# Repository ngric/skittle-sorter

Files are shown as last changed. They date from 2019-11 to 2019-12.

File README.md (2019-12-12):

# skittle-sorter

complete

## Schematics

Not so good schematic:

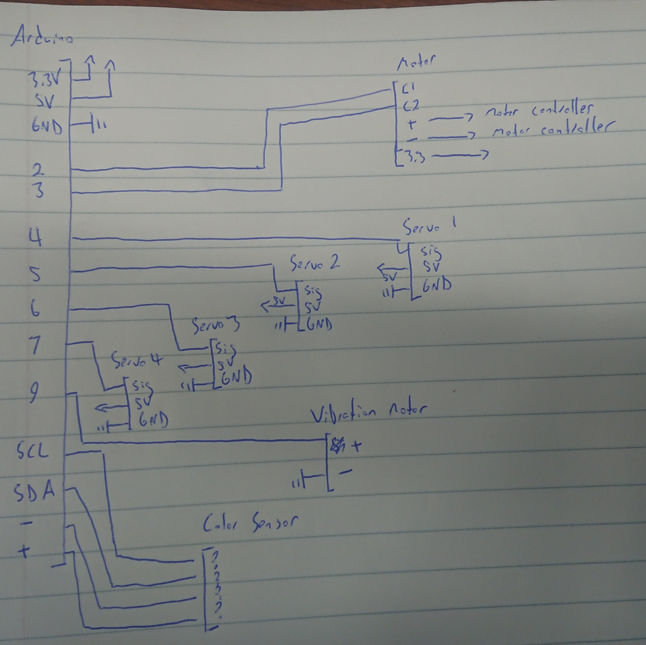
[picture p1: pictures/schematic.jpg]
schematic


Wired up:



## Auger

The centerpiece of our design was an auger, or screw of archimedes.  The skittles were supposed to be carried down a path by the auger, and then get dropped out into thier specific bins.

We went through a couple different revisions of the auger, changing the number of flights and the amount of twist. What we settled on had thwee flights, and 1500 degrees of twist. As it was too long for us to print in one piece, we split it in half then glued them together.

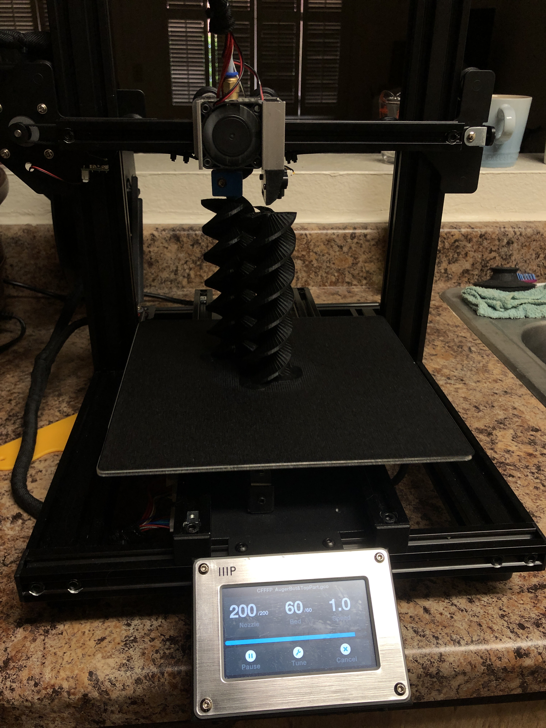
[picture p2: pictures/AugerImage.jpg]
auger printing


## Tube

The auger was contained within a tube.

The tube was split into two parts, as well, not due to length but complexity of design. The bottom section contained a hole that skittles fell into to get sorted, and an enclosure for the color sensor. The top part of the tube had four doors that skittles of specific colors were supposed to fall through.

doors

Each door needed some guides so that it would properly seat into the tube

augerthroughdoor

## Color Sensor

sensor

Our color sensor was placed at the bottom of the auger tube.
We had a lot of issues getting the sensor to read skittle color reliably. With no skittles in the chamber, we would often get readings for colors at random, regardless of how much calibration we attempted to do. Near the deadline, we found out that the sensor was starved for light, and were able to make some improvements by increasing the sensor's integration time, but we didn't get it 100% reliable. If we were to continue working on the sorter, we would likely try out different sensor chambers, and/or continue messing with the integration time, though increasing it significantly slowed down our _potential_ top sorting speed.

## Motor

The auger was powered by an encoded dc motor. Using it, we were able to count the number of steps it took for something on a specific flight of the auger to travel from the color sensor to any given door.

motor

To time it, we kept a "queue" of upcoming skittles, and the doors that should be open at any given time. Unfortunately, due to color sensing issues, we were never able to really test out the queueing.

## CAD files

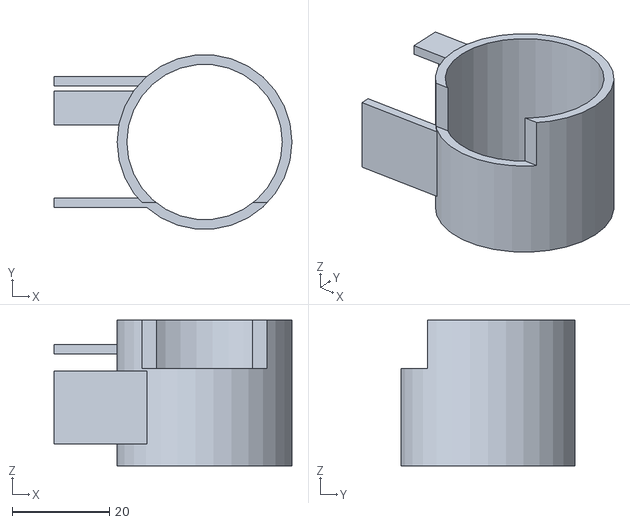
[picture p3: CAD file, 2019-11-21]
scad/clip_test_1.stl
49.0 x 35.8 x 30.0

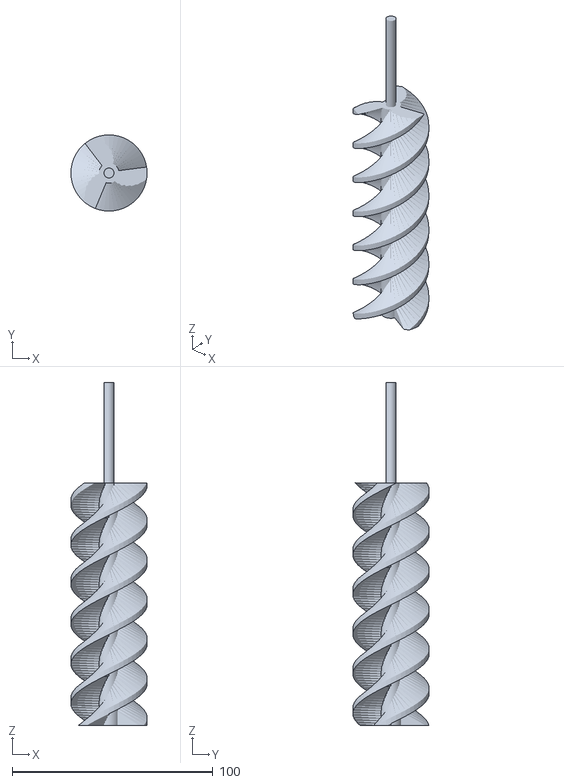
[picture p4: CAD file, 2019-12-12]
stl/AugerBotPart.stl
38.0 x 38.0 x 171.0

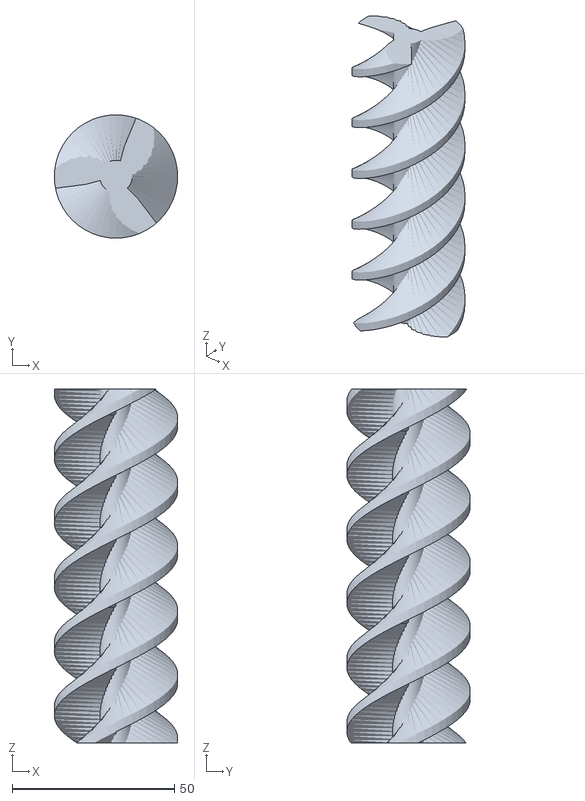
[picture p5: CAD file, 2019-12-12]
stl/AugerTopPart.stl
38.0 x 38.0 x 109.0

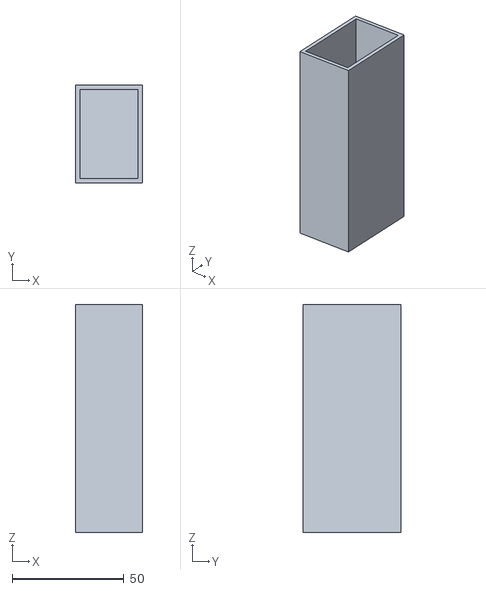
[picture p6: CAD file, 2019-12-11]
stl/SkittleBox.stl
30.0 x 44.0 x 102.0

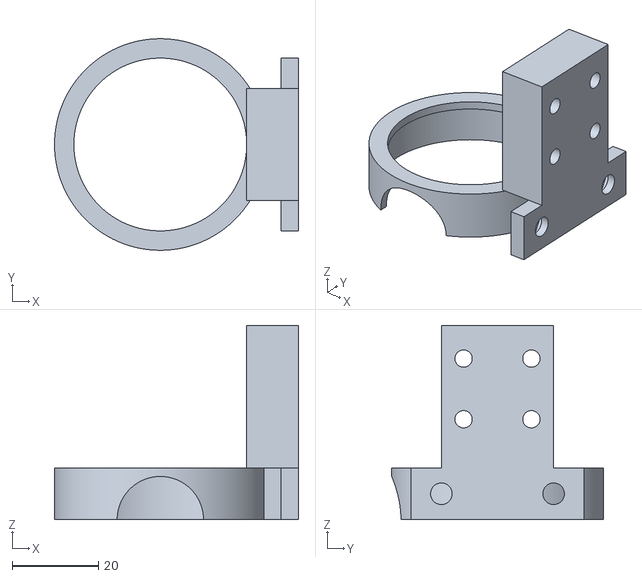
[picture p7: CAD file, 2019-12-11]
stl/motorSideMount.stl
56.5 x 49.0 x 45.0

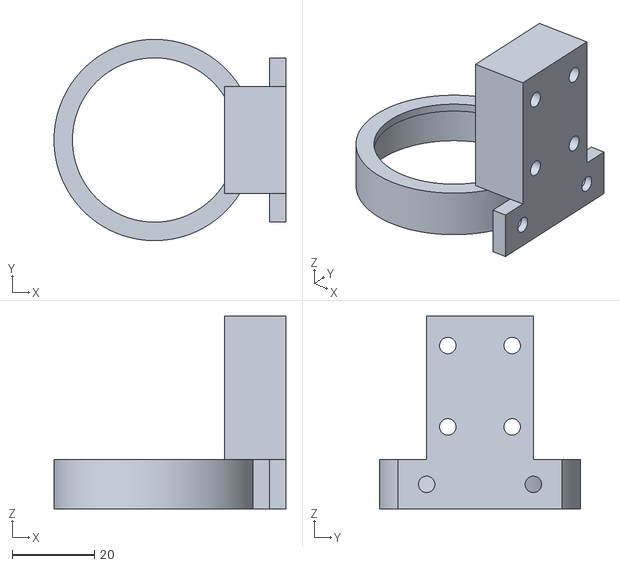
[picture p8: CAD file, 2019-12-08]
stl/mounts.stl
56.5 x 49.0 x 47.0

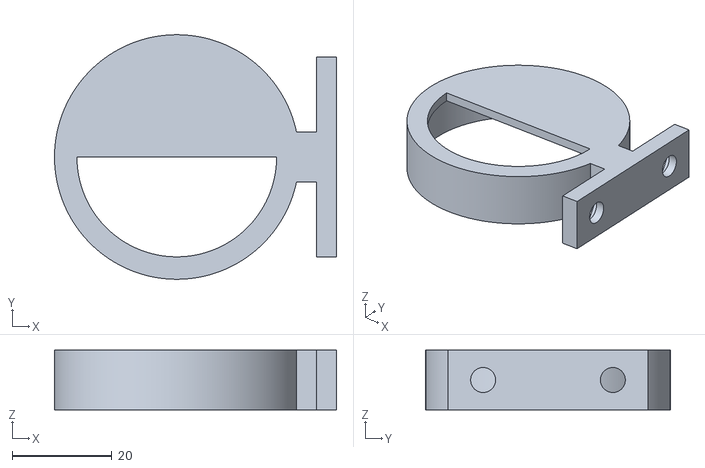
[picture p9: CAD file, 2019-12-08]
stl/augerSideMount.stl
56.5 x 49.0 x 12.0

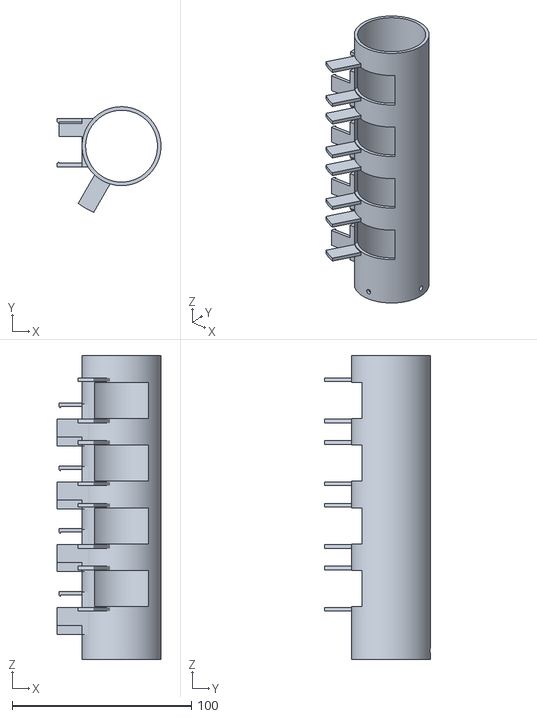
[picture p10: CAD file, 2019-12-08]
stl/tubev2.1.stl
58.0 x 58.9 x 169.5

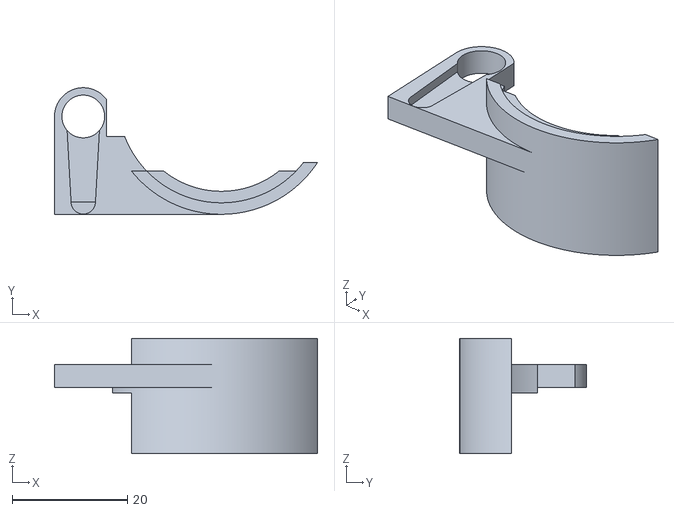
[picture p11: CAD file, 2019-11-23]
stl/door.stl
45.7 x 22.0 x 20.0

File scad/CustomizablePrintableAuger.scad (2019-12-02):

// Parametric Printable Auger
// It is licensed under the Creative Commons - GNU GPL license.
// � 2013 by William Gibson
// http://www.thingiverse.com/thing:96462

// 5 colors in skittle bag

////////////
//Examples//
////////////

//Simple Example
// auger(r1=1/8*inch, r2=.75*inch, h=1*inch, 
// turns=2, multiStart=1, flightThickness = 0.6, 
// overhangAngle=20, supportThickness=0.0);

//Multistart example
// auger(r1=1/2*inch, r2=2*inch, h=2*inch, 
// turns=1, multiStart=3, flightThickness = 0.6, 
// overhangAngle=20, supportThickness=0.0);

//Support
// auger(r1=1/2*inch, r2=2*inch, h=2*inch, 
// turns=2, multiStart=1, flightThickness = 0.6, 
// overhangAngle=10, supportThickness=0.4);


//////////////////////
//CUSTOMIZER OPTIONS//
//////////////////////

/* [Auger] */

//The total amount of twist, in degrees
Auger_twist = 1080; //[90:1080]

//The radius of the auger's "flight" past the shaft
Auger_flight_radius = 14; //[5:50]                         // == diameter of a single skittle 

//The number of "flights" 
Auger_num_flights = 3; //[1:5]

//The height, from top to bottom of the "shaft"
Auger_flight_length = 180; //[10:200]                           

/* [Printer] */

//The overhang angle your printer is capable of
Printer_overhang_capability = 30; //[0:40]

//The thickness of perimeter support material
Auger_perimeter_thickness = 0.0; //[0:None, 0.8:Thin, 2:Thick]

/* [Uninteresting] */

//The radius of the auger's "shaft"
Auger_shaft_radius = 5; //[1:25]

//The thickness of the "flight" (in the direction of height)
Auger_flight_thickness = 3;  //[0.2:Thin, 1:Medium, 10:Thick]

Auger_handedness = "right";  //["right":Right, "left":Left]

/* [Build plate] */

//for display only, doesn't contribute to final object
build_plate_selector = 3; //[0:Replicator 2,1: Replicator,2:Thingomatic,3:Manual]
//when Build Plate Selector is set to "manual" this controls the build plate x dimension
build_plate_manual_x = 200; //[100:400]
//when Build Plate Selector is set to "manual" this controls the build plate y dimension
build_plate_manual_y = 200; //[100:400]

build_plate(build_plate_selector,build_plate_manual_x,build_plate_manual_y);

/* [Hidden] */

M_PI = 3.14159;
mm = 1;
inch = 25.4 * mm;

/*---Code by Chaoneng Quan---*/
$fn = 200;
tubeHeight= Auger_flight_length - 25;


shieldHeight = 27;  //27 touching top
openRadius = 8;
openHeight = 10;


/*---end of code---*/

translate([0,0,3]) {
    difference() {
        union() {
            translate([0,0,179])rotate([180,0,0])
            auger(
                    r1 = Auger_shaft_radius,
                    r2 = Auger_shaft_radius + Auger_flight_radius,
                    h = Auger_flight_length,
                    overhangAngle = Printer_overhang_capability,
                    multiStart = Auger_num_flights,
                    flightThickness = Auger_flight_thickness,
                    turns = Auger_twist/360,
                    pitch=0,
                    supportThickness = Auger_perimeter_thickness,
                    handedness=Auger_handedness,
                    //$fn=50,
                    $fa=12,
                    $fs=5
                 );
            translate([0,0,-2])cylinder(h=3,d=5.5);
        }
        // motor shaft hole
        translate([0,0,-1])
            scale([1.05,1.05,1.05]){
                difference() {
                    translate([0,0,-3])
                        cylinder(h=15,d=4);
                    translate([1.5,-2,-3])
                        cube([4,4,15]);
                }
            }
        translate([0,0,179.5]) cylinder(h=10,r=50);
    }
}



//////////////////////
//Auger Library Code//
//////////////////////

//Notes: 
//Specify 'pitch' OR 'turns' (pitch overrides turns)
//r1 >= 1mm please
//flightThickness >= extrusion thickness of your printer
//supportThickness >= 2 * extrusion width of your printer, or zero to turn off.

module auger(r1 = 0.5*inch, r2 = 0.75*inch, h=1*inch, multiStart=1,
turns=1, pitch=0,
flightThickness = 0.2*mm, overhangAngle=20, supportThickness=0*mm,
handedness="right" /*"left"*/)
{	
	assign(_turns = ((pitch>0?h/(pitch+flightThickness):turns)))
	{
		if(pitch != 0)
		{
			echo("Pitch defined - ignoring turns parameter");
			//Each 1 turn is a height of (pitch+flightThickness)
			//A height of h will make x turns where x = h / (pitch+flightThickness)
			
			echo("Calculated turns = ", _turns);
		}
		else
		{
			if(turns < 0)
			{
				echo("ERROR: Cannot handle negative turns. Use handedness='left' instead to reverse rotation.");
			}
		}
		
		
		assign(extraFlight = tan(overhangAngle)*(r2-r1))
		{
			difference()
			{
				auger_not_truncated(r1=r1, r2=r2, h=h, turns=_turns, 
				flightThickness=flightThickness, overhangAngle=overhangAngle, 
				multiStart=multiStart, supportThickness=supportThickness,
				handedness=handedness=="right"?1:-1);
				
				//Cut off bottom of auger so it's printable.
				translate([0,0,-extraFlight])
				cube([r2 * 3,r2 * 3,2*extraFlight], center=true);
			}
		}
	}
	
}



module auger_not_truncated(r1 = 0.5*inch, r2 = 0.75*inch, h=1*inch, turns=1, flightThickness = 0.2*mm, overhangAngle=20, multiStart=1, supportThickness=0*mm, handedness=1)
{
	assign(extraFlight = tan(overhangAngle)*(r2-r1))
	{
		if(supportThickness > 0)
		{
			difference()
			{
				cylinder(h=h, r=r2+0.1, $fs=0.5);
				
				translate([0,0,-1])
				cylinder(h=h+2, r=r2-supportThickness+0.1, $fs=0.5);
			}
		}
		
		cylinder(r=r1, h=h,$fs=0.5); //Central shaft
		
		
		for(start=[1:1:multiStart]) //render each flight
		{
			rotate([0,0,handedness*360*(start-1)/multiStart])
			augerFlight(flightThickness=flightThickness, turns=turns, rHidden=(r1>6?r1-5:1), r1=r1, r2=r2, h=h, extraFlight=extraFlight, handedness=handedness);
			
		} 
	}
}
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

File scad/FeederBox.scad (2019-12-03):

//Box Feeder

$fn = 10;
//Skittle dimensions
DiameterOfSkittle = 13;
ThicknessOfSkittle = 9;

//Feeder dimensions
wallThickness = 2;


//feeder();

module feeder(){
    difference(){    
        box();
        cavity();
    }
    cover();
}

//box dimension
boxLength = 180;
boxWidth = 50;
boxHeight = 50;
module box(){
    cube([boxLength,boxWidth,boxHeight]);
}

//cavity dimension
topDiameter = boxWidth;
botDiameter = boxWidth*4/5;
//hole dimension
holeDiameter = DiameterOfSkittle + 2;

module cavity(){
    //cylinder
    rotate([0,8,0])translate([0,boxWidth/2,boxHeight])rotate([0,90,0])cylinder(d1=botDiameter,d2=topDiameter,h=boxLength);
    //hole
    translate([boxLength-holeDiameter+2,boxWidth/2,-1]) cylinder(d=holeDiameter, h= 100,$fn=100
    );
    translate([5,5,35]) cube([170,40,30]);
}

module cover(){
   translate([175,0,0])cube([5,boxWidth,boxHeight]);
}

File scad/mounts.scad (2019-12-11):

use <MCAD/regular_shapes.scad>
$fn=300;

motor_end();
//open_end(true);

// tube connection point
module ring() {
    difference() {
        cylinder(d=49, h=12);
        cylinder(d=45, h=10);
        cylinder(d=40, h=25, center=true);
    }
}

module motor_end() {
    difference() {
        open_end();
        //translate([-20,-30,0])
        //#cube([40,20,12]);
        rotate([0,90,90]) translate([0,0,-30])
            #cylinder(d=20, h=20);
    }
    difference() {
        translate([20,-13,12])
            cube([12,26,33]);
        #translate([25,7.85,23.25]) rotate([0,90,0])
            cylinder(d=4,h=20, center=true);
        #translate([25,-7.85,23.25]) rotate([0,90,0])
            cylinder(d=4,h=20, center=true);
        #translate([25,7.85,37.3]) rotate([0,90,0])
            cylinder(d=4,h=20, center=true);
        #translate([25,-7.85,37.3]) rotate([0,90,0])
            cylinder(d=4,h=20, center=true);
    }
}

module open_end(stop=false) {
    ring();
    translate([23,-5,0])
        cube([5,10,12]);
    translate([28,-20,0])
        difference() {
            cube([4,40,12]);
            hex_hole();
            translate([0,26,0]) hex_hole();
        }
    if (stop) {
        difference() {
            translate([0,0,10]) cylinder(h=2, d=40);
            #translate([-25,-20,0])cube([100,20,15]);
        }
    }
}

module hex_hole() {
    rotate([0,90,0]) translate([-6,7,0]) rotate([0,0,30]) {
        hexagon_prism(2, 5);
        cylinder(d=5,h=10);
    }
}

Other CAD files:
scad/tube.scad
scad/TubeBottomPart.scad
scad/TubeTopPart.scad

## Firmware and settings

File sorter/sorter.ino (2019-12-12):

#include <Wire.h>
#include "Adafruit_TCS34725.h"
#include <Adafruit_MotorShield.h>
#include "utility/Adafruit_MS_PWMServoDriver.h"
#include <Servo.h>

// Pins
const int encoderPin = 2;
const int servo1Pin = 4;
const int servo2Pin = 5;
const int servo3Pin = 6;
const int servo4Pin = 7;
const int vibrationPin = 9;

// Trap-door servos
Servo door[4];

// Motor Shield
Adafruit_MotorShield AFMS = Adafruit_MotorShield(); 
Adafruit_DCMotor *myMotor = AFMS.getMotor(1);

// Global
volatile int count = 0;
int lastCount = -1;
unsigned long queue = 0UL;
const int CHANGE_DELAY = 100 ;

// Servo
const int OPEN = 60;
const int CLOSED = 100;

// Example code for the Adafruit TCS34725 breakout library applied to Skittle colour classification.
// This example uses RGB vectors for classification.  It also converts the RGB vector to a HSB colourspace, 
// which is likely more robust for this classification, but does not implement the HSB classification.
// (If you change to HSB, you will likely only need hue and saturation, and not brightness). 

// More information:
// Breakout board: https://www.adafruit.com/product/1334
// Library: https://github.com/adafruit/Adafruit_TCS34725
// Installation instructions: https://learn.adafruit.com/adafruit-all-about-arduino-libraries-install-use/how-to-install-a-library

   
// Initialise TCS24725 with specific int time and gain values 
// Note: 2-4 millisecond integration (sampling) times mean we can sample at about 250-500Hz
Adafruit_TCS34725 tcs = Adafruit_TCS34725(TCS34725_INTEGRATIONTIME_24MS, TCS34725_GAIN_1X);

/*
 * Global colour sensing variables
 */

#define NUM_COLORS  6

// Skittle colours to indices
#define COL_RED     0
#define COL_GREEN   1
#define COL_ORANGE  2
#define COL_YELLOW  3
#define COL_PURPLE  4
#define COL_NOTHING 5

// Names for colours
#define COLNAME_RED     "RED"
#define COLNAME_GREEN   "GREEN"
#define COLNAME_ORANGE  "ORANGE"
#define COLNAME_YELLOW  "YELLOW"
#define COLNAME_PURPLE  "PURPLE"
#define COLNAME_NOTHING "NOTHING"

// RGB channels in the array
#define CHANNEL_R   0
#define CHANNEL_G   1
#define CHANNEL_B   2

// Training colours (populate these manually, but these vectors must be of unit length (i.e. length 1))
float trainingColors[3][NUM_COLORS];    // 3(rgb) x NUM_COLORS.

// Last read colour
float rNorm = 0.0f;
float gNorm = 0.0f;
float bNorm = 0.0f;
float hue = 0.0f;
float saturation = 0.0f;
float brightness = 0.0f;

// Last classified class
int lastClass = -1;
float lastCosine = 0;

/*
 * Colour sensing
 */
void initializeTrainingColors() {
  // Skittle: red
  trainingColors[CHANNEL_R][COL_RED] = 0.828;
  trainingColors[CHANNEL_G][COL_RED] = 0.415;
  trainingColors[CHANNEL_B][COL_RED] = 0.374;

  // Skittle: green
  trainingColors[CHANNEL_R][COL_GREEN] = 0.537;
  trainingColors[CHANNEL_G][COL_GREEN] = 0.762;
  trainingColors[CHANNEL_B][COL_GREEN] = 0.360;

  // Skittle: orange
  trainingColors[CHANNEL_R][COL_ORANGE] = 0.921;
  trainingColors[CHANNEL_G][COL_ORANGE] = 0.326;
  trainingColors[CHANNEL_B][COL_ORANGE] = 0.210;

  // Skittle: yellow
  trainingColors[CHANNEL_R][COL_YELLOW] = 0.690;
  trainingColors[CHANNEL_G][COL_YELLOW] = 0.659;
  trainingColors[CHANNEL_B][COL_YELLOW] = 0.296;

  // Skittle: purple
  trainingColors[CHANNEL_R][COL_PURPLE] = 0.8586;
  trainingColors[CHANNEL_G][COL_PURPLE] = 0.3487;
  trainingColors[CHANNEL_B][COL_PURPLE] = 0.3758;

  // Nothing
  trainingColors[CHANNEL_R][COL_NOTHING] = 0.6729;
  trainingColors[CHANNEL_G][COL_NOTHING] = 0.5633;
  trainingColors[CHANNEL_B][COL_NOTHING] = 0.4794;
}


void getNormalizedColor() {
  uint16_t r, g, b, c, colorTemp, lux;  
  tcs.getRawData(&r, &g, &b, &c);
  Serial.print("RAW: ");
  Serial.print(" R: "); Serial.print(r);
  Serial.print(" G: "); Serial.print(g);
  Serial.print(" B: "); Serial.println(b);
  Serial.println();

  float lenVec = sqrt((float)r*(float)r + (float)g*(float)g + (float)b*(float)b);

  // Note: the Arduino only has 2k of RAM, so rNorm/gNorm/bNorm are global variables. 
  rNorm = (float)r/lenVec;
  gNorm = (float)g/lenVec;
  bNorm = (float)b/lenVec;

  // Also convert to HSB:
  RGBtoHSV(rNorm, gNorm, bNorm, &hue, &saturation, &brightness);
}


int getColorClass() {
  float distances[NUM_COLORS] = {0.0f};

  // Step 1: Compute the cosine similarity between the query vector and all the training colours. 
  for (int i=0; i<NUM_COLORS; i++) {
    // For normalized (unit length) vectors, the cosine similarity is the same as the dot product of the two vectors.
    float cosineSimilarity = rNorm*trainingColors[CHANNEL_R][i] + gNorm*trainingColors[CHANNEL_G][i] + bNorm*trainingColors[CHANNEL_B][i];
    distances[i] = cosineSimilarity;

    // DEBUG: Output cosines
    //Serial.print("   C"); Serial.print(i); Serial.print(": "); Serial.println(cosineSimilarity, 3);
  }

  // Step 2: Find the vector with the highest cosine (meaning, the closest to the training color)
  float maxVal = distances[0];
  int maxIdx = 0;
  for (int i=0; i<NUM_COLORS; i++) {
    if (distances[i] > maxVal) {
      maxVal = distances[i];
      maxIdx = i;
    }
  }

  // Step 3: Return the index of the minimum color
  lastCosine = maxVal;
  lastClass = maxIdx;
  return maxIdx;
}


// Convert from colour index to colour name.
void printColourName(int colIdx) {
  switch (colIdx) {
    case COL_RED:
      Serial.print(COLNAME_RED);
      break;
    case COL_GREEN:
      Serial.print(COLNAME_GREEN);
      break;
    case COL_ORANGE:
      Serial.print(COLNAME_ORANGE);
      break;
    case COL_YELLOW:
      Serial.print(COLNAME_YELLOW);
      break;
    case COL_PURPLE:
      Serial.print(COLNAME_PURPLE);
      break;
    case COL_NOTHING:
      Serial.print(COLNAME_NOTHING);
      break;
    default:
      Serial.print("ERROR");
      break;
  }
}

// RGB to HSV.  From https://www.cs.rit.edu/~ncs/color/t_convert.html . 
void RGBtoHSV( float r, float g, float b, float *h, float *s, float *v ) {  
  float minVal = min(min(r, g), b);
  float maxVal = max(max(r, g), b);
  *v = maxVal;       // v
  float delta = maxVal - minVal;
  if( maxVal != 0 )
    *s = delta / maxVal;   // s
  else {
    // r = g = b = 0    // s = 0, v is undefined
    *s = 0;
    *h = -1;
    return;
  }
  if( r == maxVal )
    *h = ( g - b ) / delta;   // between yellow & magenta
  else if( g == maxVal )
    *h = 2 + ( b - r ) / delta; // between cyan & yellow
  else
    *h = 4 + ( r - g ) / delta; // between magenta & cyan
  *h *= 60;       // degrees
  if( *h < 0 )
    *h += 360;
}

/*
 * Main Arduino functions
 */
 
void setup(void) {
  Serial.begin(115200);

  // Populate array of training colours for classification. 
  initializeTrainingColors();
  
  if (tcs.begin()) {
    Serial.println("Found sensor");
  } else {
    Serial.println("No TCS34725 found ... check your connections");
    while (1);
  }
  
  // Now we're ready to get readings!

    pinMode(encoderPin, INPUT);
    attachInterrupt(digitalPinToInterrupt(encoderPin), encoderStep, FALLING);

    AFMS.begin();
    myMotor->setSpeed(60);
    myMotor->run(FORWARD);
    delay(CHANGE_DELAY);

    door[0].attach(servo1Pin);
    door[1].attach(servo2Pin);
    door[2].attach(servo3Pin);
    door[3].attach(servo4Pin);

    pinMode(vibrationPin, OUTPUT);
    analogWrite(vibrationPin, 255);

    door[0].write(OPEN);
    door[1].write(OPEN);
    door[2].write(OPEN);
    door[3].write(OPEN);
}

void loop(void) {
    // Step 1: Get normalized colour vector
    getNormalizedColor();
    int colClass = getColorClass();   

    #ifdef DEBUG
    delay(24);
    // Step 2: Output colour
    Serial.print("R: "); Serial.print(rNorm, 3); Serial.print("  ");
    Serial.print("G: "); Serial.print(gNorm, 3); Serial.print("  ");
    Serial.print("B: "); Serial.print(bNorm, 3); Serial.print("  ");  
    Serial.print("H: "); Serial.print(hue, 3); Serial.print("  ");
    Serial.print("S: "); Serial.print(saturation, 3); Serial.print("  ");
    Serial.print("B: "); Serial.print(brightness, 3); Serial.print("  ");
     
    printColourName(colClass);  
    Serial.print(" (cos: "); Serial.print(lastCosine); Serial.print(") ");
    Serial.println("");
    #endif

    enqueue(colClass);

    if (count == lastCount) {
        Serial.print("Last: "); Serial.print(lastCount); Serial.print("Count: "); Serial.println(count); 
        unjam();
    } else {
        lastCount = count;
    }

    if ( count > 125) {
      count = 0;
      queue = (queue >> 4) & 0x7FFFF;
      Serial.print("Queue: "); Serial.println(queue, BIN);
      readQueue();
    }
}

void unjam() {
    int tmp = count;
    myMotor->run(BACKWARD);
    delay(CHANGE_DELAY);
    myMotor->run(FORWARD);
    delay(CHANGE_DELAY);
    noInterrupts();
    count = tmp;
    lastCount = count -1;
    interrupts();
}

void enqueue(int colClass) {
    if (colClass == 0) { //red
        bitSet(queue, 8);
    } else if (colClass == 1) { //green
        bitSet(queue, 13);
    } else if (colClass == 2) { //orange
        bitSet(queue, 18);
    } else if (colClass == 3) { //yellow
        bitSet(queue, 23);
    }
}

void readQueue(){
    for (int i = 0; i < 4; i++) {
        if (bitRead(queue, i)) {
            door[i].write(OPEN);
        } else {
            door[i].write(CLOSED);
        }
    }
}

void encoderStep() {
    count++;
}

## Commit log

2019-11-20 Added auger librarary
    [Auger1_Left.stl, Auger1_Right.stl, Auger2.stl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]
2019-11-20 cleanup directory
    [Auger1_Left.stl, Auger1_Right.stl, Auger2.stl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]
2019-11-20 Added auger file
    [CustomizablePrintableAuger.scad, CustomizablePrintableAugerscad.scad]
2019-11-21 prototype servo attachment point
    [CustomizablePrintableAuger.scad, build_plate.scad, clip_test_1.stl]
2019-11-21 working (blue) servo clip
    [CustomizablePrintableAuger.scad, testClipBlue.stl]
2019-11-21 move stl to new dir
    [testClipBlue.stl]
2019-11-23 tube v1.0
    [CustomizablePrintableAuger.scad, tube_v1.stl]
2019-11-23 door v1
    [CustomizablePrintableAuger.scad, door.stl]
2019-11-24 space holes further apart
    [CustomizablePrintableAuger.scad]
2019-11-24 move up top servo stop, add snap
    [CustomizablePrintableAuger.scad, testClipBlue.stl]
2019-11-25 tighten clips, tube v1.1
    [CustomizablePrintableAuger.scad, testClipBlue.stl, tube_v1.1.stl]
2019-11-26 motor specs
2019-11-27 up id of tube to 38mm, clips and holes still unadapted
    [38dtube.stl, CustomizablePrintableAuger.scad]
2019-11-28 motor and encoder poc
    [Auger4Flights.stl]
2019-11-29 mess with servos in addition to motor
2019-12-02 adjust servo clip position
    [38dTestSection.stl, CustomizablePrintableAuger.scad]
2019-12-02 further resizing, door needs further adjustment
    [CustomizablePrintableAuger.scad, tube.scad]
2019-12-03 pull feederbox and tubebottom from augerandshield branch
    [FeederBox.scad, TubeBottomPart.scad]
2019-12-03 remove auger4flignts
    [Auger4Flights.scad]
2019-12-04 Make motor move always forward
2019-12-05 merged color sensor code
2019-12-07 tubetoppart from augerandshield branch
    [TubeTopPart.scad]
2019-12-08 tube mounts
    [TubeTopPart.scad, augerSideMount.stl, motorSideMount.stl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]
2019-12-11 widen skittle hole cutout on tube mount
    [SkittleBox.stl, motorSideMount.stl, mounts.scad]
2019-12-12 clean up stls
    [38dTestSection.stl, 38dtube.stl, Auger4Flights.stl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]
2019-12-12 add schematic
